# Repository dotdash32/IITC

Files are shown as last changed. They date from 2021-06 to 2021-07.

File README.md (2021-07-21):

# IITC

Intra- and Inter- Tool Changer for Budget 3D Printers

Designed as a mostly printable add-on to the Ender 3 or other V-slot based machines.

The IITC is designed to be cheap to make, widely capable, and easily modifiable.  As such, this Github includes the STLs to print the device, as well as the Fusion 360 files used to create them.

Tech Demo (http://www.youtube.com/watch?v=5y99OYjvCSE)

## Current Progress

The files are currently in development!  While everything *mostly* works on my machine, there are printability and longevity improvements going on.  See the Projects page for a more up to date version of current progress.

## Features

While none of these ideas are completely novel, the combination of these creates a new and very capable machine.

### Intra- Tool Changes

Intra tool changes are between tools on the same tool group, or head.  This is facilitated by the tilting of the head back and forth, and is similar to [MakerTech 3D's Dual Switching Extruder](https://www.makertech3d.com/products/dual-switching-extruder-non-proforge).  Inside a job, this is the most common type of tool change, and is done with just GCode commands.

It rides on bearings for smooth operation and longevity of printed parts.  It uses a kinematic mount, inspired by the [E3D ToolChanger](https://e3d-online.com/pages/toolchanger), but uses socket head cap screws (SHCS) to reduce cost and mounting space.  With entirely standard components, a highly repeatable attachment platform is made.

### Inter- Tool Changes

Inter tool changes are between different tool groups.  These are manually facilitated, allowing the machine to change between different types of tools.  Switching out symmetric nozzles for a dedicated flexible hot end, or mounting a laser engraver or pen plotter.  This is similar to the [XChange](https://www.kickstarter.com/projects/printermods/xchange-v10-hot-swap-tool-changing-for-every-3d-printer) or [Mutant](https://whambamsystems.com/mutant).  However, this combines with the Intra switches to have a more capable machine.

### Tool Ecosystem

The kinematic mount and angle are the same between 1, 2, and 4 position mounts.  Tool groups can still be used on mounts with fewer or more positions, so tool groups are compatible between machines even if they have different numbers of extruders enabled.  This is intended so that a shop with multiple printers can expand flexible capacity without needing to upgrade every mainboard to dual extrusion.

### Remote Tool Changes

A Bowden style servo actuates the tilting motion through a wire rope and spring guides.  The mass of the servo is moved to the rigid frame, thus reducing the mass of the toolhead.  This is inspired by the [Jubilee](https://jubilee3d.com/index.php?title=Main_Page), and uses similar parts.  

### Automatic Z Probing

The kinematic mount gives the Inter tool changes high repeatability, but when spring loaded, the kinematic mount acts like a [Renishaw CNC probe](https://www.renishaw.com/en/kinematic-mounts--25938).  Thus, the nozzle can be used as a probe like a CR-6 and detect any bed surface.

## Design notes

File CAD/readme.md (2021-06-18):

# CAD

The CAD models of the project!

Files are organized by subassembly.
The computer these were designed on is 6 years old and can't handle very large files, so most things are split up for ease of use and modeling.
Each folder contains approximately one assembly with the structure:

```
+-- Assembly_Name_1
|   +-- 0Assembly_Name_1.f3d
|   +-- STL_File1.stl
|   +-- STL_File2.stl
|   +-- readme.md
+ -- Assembly_Name_2
|   +-- ....
+ -- Tools
|   +-- Tool_Name_1
|   |  +-- 0Tool_Name_1.f3d
|   |   +-- STL_File1.stl
|   |   +-- STL_File2.stl
|   |   +-- readme.md
|   +-- Tool_Name_2
|   |   +--...
```

Each folder contains the Fusion archive that was used to make it, so some of these files are `.f3z`, Fusion's interdependent format since they contain derived parts.
Each STL is labelled, but they might not have 1-1 correspondence with Component names.
Instead, there should be nearly 1-1 correspondence on Body names, which is easier for export and managing.

WARNING: Body renaming is still in progress, so it might not be perfect.  If it's unclear, please submit an issue!

Each folder readme should include the needed materials, which will also be compiled in a general spreadsheet to easily build BOMs.  This is a work in progress (yikes), and should also include assembly instructions soon.

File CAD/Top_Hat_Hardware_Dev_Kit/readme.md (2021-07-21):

# Top Hat Hardware Dev Kit

Files related to the Kinematic Mount and creating new tools.  Included are STEP and Fusion files of a simplified mount.
The files contain the `Top_Hat` in it's unmodified form, as well as the infrastructure it mounts to.

The E plate and moving mount are included, but at lower detail so less powerful computers (aka Dotdash's) can create add-ons more easily.
These files are intended to simplify and ease the creation of new tools.
Rather than needing the supply side (Dotdash) to create them, please make your own and pull request them in!

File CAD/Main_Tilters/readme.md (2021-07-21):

# Main Tilters

The main bulk of the project is here, these are what do the dirty work.
There are 3 possible combinations, and each need slightly different materials.

## Common Parts

This topmost section is common to all tilters, so any set of tools can be attached to any tilter.
This is the Kinematic Mount, the set of six screw heads (SHCS) that create a unique resting position for the tool groups mating screws.

### Common Needed Materials

* 1x `Nut_Trap`
* 6x 8mm M3 SHCS
* 6x Thin M3 Nuts

## 1 Position Tilter

This tilter doesn't move, but gives any printer Inter-changes and automatic probing for just a few parts.
Two options, depending on which side of the tool should be used.
This enables a simpler machine to still run complex tool groups, just one tool at a time.

<!-- ![1 Pos Right](/images/1_Pos_Right.png){:width="10px"} ![1 Pos Left](/images/1_Pos_Left.png) -->

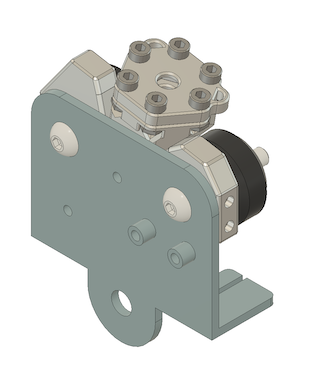
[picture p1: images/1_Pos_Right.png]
1_Pos_Right

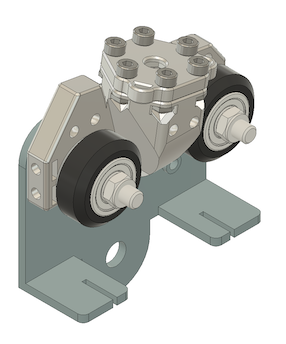
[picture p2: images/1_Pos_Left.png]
1_Pos_Left


### 1 Pos Needed Materials

* 1x `1_Pos_Main_XXX`
  * `_Right` is the near-stock hot end configuration for the Ender 3
  * `_Left` is the `T0` position for the 2 position holder.

Why are there those weird side sections? They extend from the largest flat plane downward, removing the need for supports.

## 2 Position Tilter

This is the mainstay of the project, 2 tools per tool group for intra-switches.

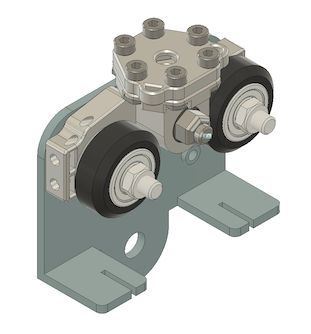
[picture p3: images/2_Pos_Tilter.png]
2 Pos Tilter


### 2 Pos Needed Materials

* 1x `2_Pos_Main`
* 1x `Stationary_Mount`
* 1x `Bearing_Internal_Spacer`
* 1x 25mm M5 FHS
* 2x 105zz Bearings
* 1x Nylock M5 Nut
* 1x 5mm M3 SHCS

### 2 Pos Optional Back Brace

An experimental feature, add 1x `2_Pos_Back_Brace` to potentially stiffen the tilting mechanism.  This is being tested, but requires support and hasn't shown a significant difference in performance yet.

## 4 Position Tilter

This is not finished!
But in order to keep this option open, it needs to be at least partially designed for from the start.
It does not currently have provisions for a tilting cable, but that will hopefully change soon.

This enables front and back tilting as well, so 2 Position Tool Groups will work natively as well.
The issue is that it extends back and would collide with the vertical 2040 beams on the Ender 3.

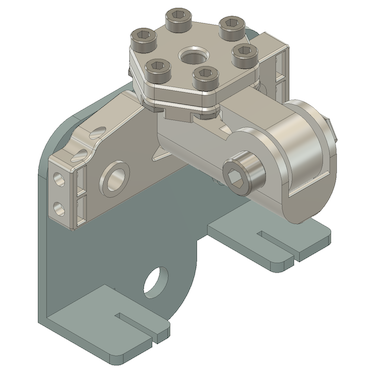
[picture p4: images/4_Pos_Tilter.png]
4 Pos Tilter


### 4 Pos Needed materials

* 1x `4_Pos_Lower`
* 1x `4_Pos_Upper`
* 1x `Stationary_Mount`
* 2x `Bearing_Internal_Spacer`
* 1x 25mm M5 FHS
* 1x 20mm M5 SHCS
* 4x 105zz Bearings
* 2x Nylock M5 Nut
* 1x 5mm M3 SHCS (will probably become 2)

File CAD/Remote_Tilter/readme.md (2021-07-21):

# Remote Tilter

STLs for Remote tilter, uses a servo to actuate the tool change.
Mounts to Nema-17 standard pattern (i.e. to default E3 extruder position)

## 35kg Servo

The current model uses a 35kg-cm servo, which is definitely over powered for the application.  
This is to avoid overheating and failure that was observed in [TeachingTech's Switching Nozzle Video](https://www.youtube.com/watch?v=ag7b9jOhlPY).

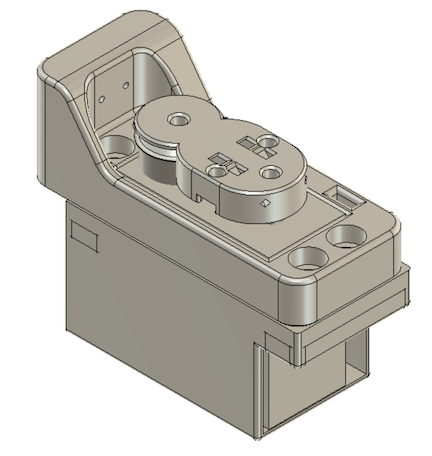
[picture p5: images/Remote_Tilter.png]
Remote Tilter


Future upgrades include testing to switch to a 20kg-cm servo which is half the price, or using a stalled DC motor with current limiting.
Other heat mitigation strategies include a 30mm fan, which has an included duct to redirect the air closely around the servo, or spare stepper motor heat sinks on the metal casing.

### Needed Materials

<!-- TODO: update this in main assembly file. -->

* 1x `Servo_mount`
* 1x `Horn_Top_Attachment`
* Nut mount system
  * 1x `Fanless_Nut_Keeper`

  OR
  * 1x `30mm_Fan_Mount`
  * 1x3010 Fan
* 1x 12mm M3 SHCS
* 5x 8mm M3 SHCS
* 4x Thin M3 Nuts
* 4x 16mm M4 SHCS
* 4x Std M4 Nuts
* 1x Standard Size RC Servo (tested with Annimos 35kg)
* 1x JST to Servo connection Cable
* 2x Spring Guides (from main assembly)

## Direct without Horn

An old version of the servo mount.
It mounts directly to the 25 tooth servo gear, hence the "Direct" name.
Needs either high precision, or to melt the teeth profile in.
This model is harder to work with, so is not fully supported, and is included for the sake of completeness, not convenience.

To melt, something like acrylic cement (for PLA, not recommended plastic) can be used.
Apply the cement liberally to the point of indentation, and then press onto the servo gear.
Let it set until dry, and you have a nice set of embedded teeth!

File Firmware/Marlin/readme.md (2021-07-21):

# Marlin Firmware Setup

## Sample Configs

Dotdash32's configs are available on their fork of [MarlinFirmware](https://github.com/dotdash32/Marlin).  Specifically of interest are the (mostly) updated and designed versions to run this tool changer for the [SKR 2](https://github.com/dotdash32/Marlin/tree/Ender3_skr2) and before it broke, [SKR 1.4T](https://github.com/dotdash32/Marlin/tree/Ender3_skr14Turbo).

There are also bug-fix branches, but are not always updated unless Dotdash has a problem and needs to submit a bug report.

## How to Setup your own Config (1 Position)

These are the key elements to enable in order to get the tool changer up and running.  It's not possible to have an example config for every board (and hard to check if they work on a student budget :\\ ).  While every configuration will be different, these will hopefully give a good guide to get started.  It is recommended that you start with a configuration that works for your printer and controller board BEFORE you start changing things.

This section describes changes needed to enable Inter Changes, switching between different tool groups.  For a single position tool changer (Inter only), follow this section (1 Pos). For a Inter and Intra tool changer, also read the following sections (2 Pos).

Marlin currently only supports up to 2 Positions, since the main element (`SWITCHING_NOZZLE`) only supports 2 positions.  If there is need for more tools (i.e. 4 Position tilter), a more expandable system like RRF or Klipper is ideal, since they can handle secondary control boards.

### Configuration.h (1 Pos)

- Enable Adjustable Temp Sensors

  - `#define TEMP_SENSOR_0 1000` This can then be changed with `M305` in each GCode tool offset file
  
- Adjust Min and Max Temps
  - Change `#define HEATER_X_MINTEMP  nnn` and `#define HEATER_X_MAXTEMP nnn` to reflect the extremes of ALL tools.  This does decrease safety, but is one cost of having only some settings at compile.

- Ensure Thermal Protections

  - `#define THERMAL_PROTECTION_HOTENDS`.  This is really important for safety!  Especially with pluggable hot ends, if a cable is loose, this can prevent fires.

- Probe Settings (For Kinematic Mount Probing)

  - Set Pin (`#define Z_MIN_PROBE_USES_Z_MIN_ENDSTOP_PIN` if using Z end stop)

  - `#define FIX_MOUNTED_PROBE` (technically that or `#define NOZZLE_AS_PROBE`, but that has more restrictions)

  - `#define NOZZLE_TO_PROBE_OFFSET { 0, 0, 0}`, this will be changed by each GCode file (especially the Z offset)

  - `#define Z_AFTER_PROBING 5` or some other value.  This is important to ensure that the tool doesn't switch too close to the bed and smash a tool into the bed

  - `#define Z_PROBE_LOW_POINT -2` or similar value to give some negative travel room

  - `#define Z_AFTER_HOMING 5` like `Z_AFTER_PROBING`, keeps nozzle from smashing into the bed

- Homing and Offsets

  - `#define Z_AFTER_HOMING 5` (it's technically in the homing section of config.h)

  - `#define Z_MIN_POS -2` Allow secondary tools to have a negative Z offset

  - `#define MANUAL_Z_HOME_POS 0` Set home position at probe trigger point

  - `#define Z_SAFE_HOMING` Required for homing with a probe

- SD Card

  - `#define SDSUPPORT` Use an SD card to store tool offset GCode files

### Configuration_adv.h (1 Pos)

- Adjustable Temp Sensors

  - Check Temp Sensor 1000 values, but will be set in GCode files

- SD Card (tool offset folder)

  - `#define SD_PROCEDURE_DEPTH 2`, allow access 1 folder down

  <!-- - `#define SD_MENU_CONFIRM_START` (optional, but incredibly useful, IMO) -->

- Baby Stepping

  - `#define BABYSTEPPING`

  - TODO: `#define BABYSTEP_XY` does this help?

<!-- - Emergency Parser

  - `#define EMERGENCY_PARSER`, Not required, but useful. -->

- Custom Menu

  - Not required, but pretty useful if you need to switch a bunch of hot ends often.

  - Either `#define CUSTOM_MENU_MAIN` or `#define CUSTOM_MENU_CONFIG`

## Intra Tool Changes Config (2 Position)

Further changes needed to enable servo switching of tools (Intra changes).  This does require a controller board capable of driving at least 2 extruder steppers and a servo.

### Configuration.h (2 Pos)

- Enable Switching Nozzle

  - `#define EXTRUDERS 2` Enable dual extrusion

  - `#define SWITCHING_NOZZLE` Specific tool change methodology

  - `#define NUM_SERVOS 1` (or 2 if also using BL Touch)

  - `#define SERVO_DELAY { 150 }` or change to fit your servo's speed

  - `#define EDITABLE_SERVO_ANGLES` This makes it much faster to dial in settings
  
- Enable Adjustable Temp Sensors

  - `#define TEMP_SENSOR_1 1000` Enable second custom thermistor

- Enable Separate PID settings

  - `#define PID_PARAMS_PER_HOTEND` Allow non-symmetric hot end control loops

  - Change `DEFINE_Kn_LIST` to 2 entries for each of the three settings.

- Enable second extruder

  - `#define E1_DRIVER_TYPE` to be whatever is in your controller board.

  - `#define DISTINCT_E_FACTORS` for non-symmetric extruders

  - Update "default values" to include 5 values.  There are several, so be sure to check them all.

    - `DEFAULT_AXIS_STEPS_PER_UNIT`

    - `DEFAULT_MAX_FEEDRATE`

    - `DEFAULT_MAX_ACCELERATION`

### Configuration_adv.h (2 Pos)

- Tool Change Raise

  - `#define TOOLCHANGE_ZRAISE 2` or other setting to clear any parts

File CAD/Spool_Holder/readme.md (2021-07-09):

# Spool Holder

Colloquially called the "Spool Whale" because of the whale tail like design, a purpose built dual spool holder with provisions for in line filament runout sensors and dual Creality style extruders.

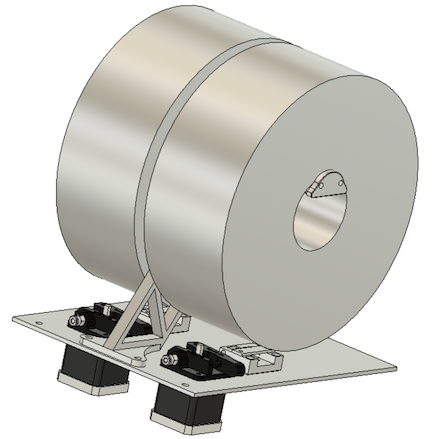
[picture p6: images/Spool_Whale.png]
Spool Whale


## Base Holder

Simple holder, includes two extruder mounts (Creality MK10 style) and dual roll filament holder.

This also adopts the PTFE liner from Voron, so that spools are not in contact with printed plastic, but instead slippery PTFE during printing.

### Needed Materials

- `Bottom_Board_Small` (dxf to be laser cut)
  - printable STL Coming Soon
- `Spool_Whale_Lower`
- `Spool_Whale_Upper`
- 2x 12mm M5 SHCS
- 2x M5 T nuts (from stock spool holder)
- 3x 12mm M3 SHCS
- 3x M3 thin nuts
- 2x Creality Extruders (steppers, extruder tops)
- 2x Bowden Tubes

## Optional Filament Runout Sensors

This is for one sensor, so for two, double everything.

### Needed materials

- `Fil_Runout_Bottom`
- `Fil_Runout_Top`
- 4x 12mm M3 SHCS
- 4x M3 thin nuts
- Short PTFE tube
- Microswitch with roller lever
- Wiring harness

There are some printability problems with the filament runout sensors relating to the Bowden tubes, so be warned.

Also, an upgrade to BMG style extruders is soft-planned for higher performance.

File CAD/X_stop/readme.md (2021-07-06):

# X Stop

A modified X limit switch holder to increase clearance.

The stock Ender 3 X stop has a QR code and sticks out really far.  This is a clearance problem for some dual extruders, since the part needs to swing out of the way during tool changes.

### Needed Materials

- 1x `Slim_X_Stop`
- 1x X stop micro switch
- 2x 5mm M3 SHCS
- 4x 25mm M3 Flat Head Screws

## Supported Version

Older version that needs support to print.
This model is more useful if you only have short SHCS (I had an Amazon mixed bag for prototyping) on hand, but otherwise, use the more updated version and the countersunk screws.

### Needed Materials

- 1x `Slim_X_Stop_Support`
- 1x X stop micro switch
- 2x 5mm M3 SHCS
- 4x 12mm M3 SHCS

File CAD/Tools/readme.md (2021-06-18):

# Tools

Different tool heads for the IITC

## Included Options:

### Common

Common tools between all options.

- `Camera_mount`: Mount for 5mm Borescope with provisions for cable management at the top.  Requires support.

- `Triple_springs`: adapt 3 light springs (McMaster #9657K622) for heavier tools.

### Single_Hero_Me

Mount for a single extruder (1Pos style).  It adapts the Hero Me Gen 3 and 9-pin D sub connector.  Mounts Creality style hot end nearly in line with original position, moves a few mm forward in Y.  No loss of X travel.

### Double_Hero_me

Mount for double extruder (2Pos style).  Adapts Hero Me Gen 3 and mirrors across to get two extruders with an approximate 38mm offset.  Uses 2 Creality hot ends and has special fan duct to avoid collisions.

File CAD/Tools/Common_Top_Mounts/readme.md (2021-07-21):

# Common Tools - Top Mounts

Common tools to mount a tool group to the base pivot.  These usually hold springs to allow for auto Z probing.

## Triple Springs Static

Adapter to use 3 McMaster #9657K622 springs for a heavier tool.

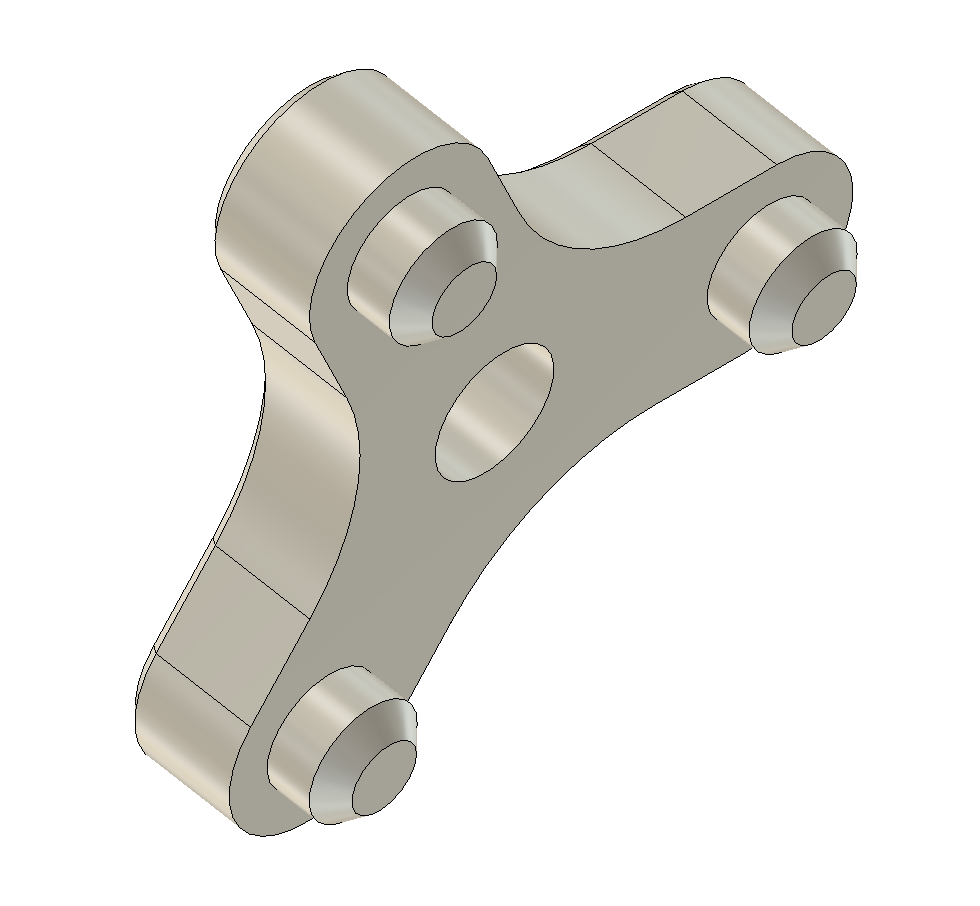
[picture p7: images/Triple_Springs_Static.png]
Triple Springs Static


### Needed Materials (Static)

- 1x `Triple_Springs_Static`
- 3x .375x.300 springs (McMaster #9657K622)
- 1x 30mm M5 (for connecting to Kin Mount)
- 1x M5 nylock nut (for connecting to Kin Mount)

## Triple Springs Adjustable

Adapter to use 3 McMaster #9657K622 springs for a heavier tool, but allow uneven forward/back tension.  This is intended to account for 2 Position tool groups, where there is significant weight on the front of the carriage, but none in the back.

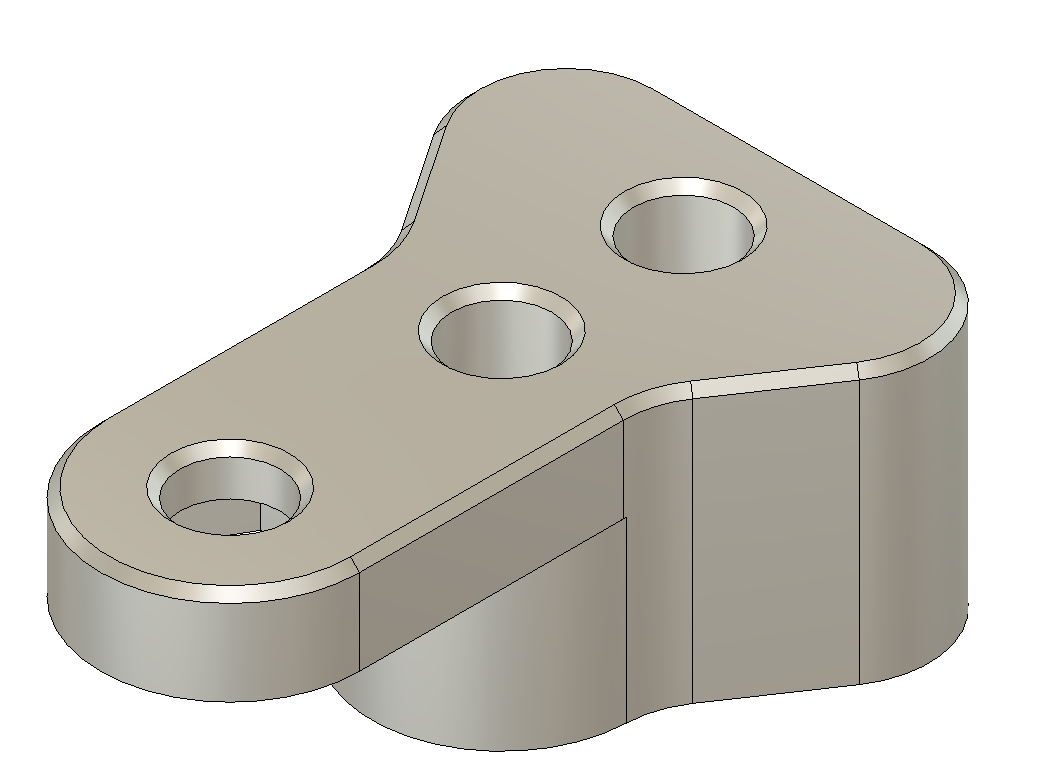
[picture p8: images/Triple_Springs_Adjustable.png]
Triple Springs Adjustable


Primary tension is adjustable with the main screw, tightening the back two springs.  Front tension is adjustable with separate jam nuts.

### Needed Materials (Adjustable)

- 1x `Triple_Springs_Adjustable`
- 3x .375x.300 springs (McMaster #9657K622)
- 1x 30mm M5 (for main connection to Kin Mount)
- 1x 20mm M5 (for rear connection to Kin Mount)
- 1x 16mm M5 (for front tension adjustment)
- 1x M5 nylock nut (for main connection to Kin Mount)
- 4x M5 thin nut (tension adjustment)

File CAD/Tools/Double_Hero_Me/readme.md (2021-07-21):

# Double Hero Me

Dual Extruder mount for 2 Creality MK8 Style hot ends

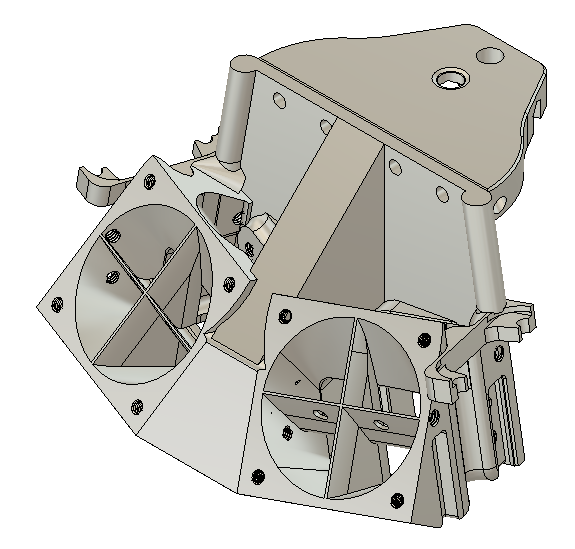
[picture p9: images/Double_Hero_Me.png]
Double_Hero_Me


## Caveats

This is sort of a legacy tool group, stitched together quickly for expedited testing.  It absolutely works, but most things are at slight angles, and the hot end mount on the right isn't the same length to the D-sub connector.  It is harder to print (support needed), and the fans are not optimized.

### Needed Materials

- 1x `Hotend_Mount`
- 1x`Top_Hat`
- 2x Creality MK8 Hot ends
- 2x 40mm Fan
- 2x Bowden tubes
- 1x `Dsub_Cap_left`
- 1x `Dsub_Cap_right`
- 2x 9 Pin D sub connectors (male)
- 1x `Fan_Duct`
- 2x 4010 Blower fans (part cooling)
- 4x 8mm M3 SHCS
- 3x 5mm M3 SHCS
- 4x 16mm M3 SHCS
- 7x Thin M3 nuts

## Hot End Modifications

To have quick change-ability for PTFE lined hot ends, it is recommended to do the "washer fix" that adds a section of captive PTFE tube inside the hot end, trapped below a washer.  This allows the Bowden tube above the washer to be easily removed without worrying about perfectly re-seating the tube after an Inter tool change.

Originally by Luke Hatfield, [CHEP has a video](https://www.youtube.com/watch?v=7tCxO17XZtw) about it, and you can find the necessary files on [Thingiverse](https://www.thingiverse.com/thing:3203831).  The fix can also improve printing overall, so its recommended to do.

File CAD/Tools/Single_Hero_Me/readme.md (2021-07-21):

# Single Hero Me

Adapted Hero Me V3 mount to mount a single Creality MK8 hot-end to the Kinematic Mount.

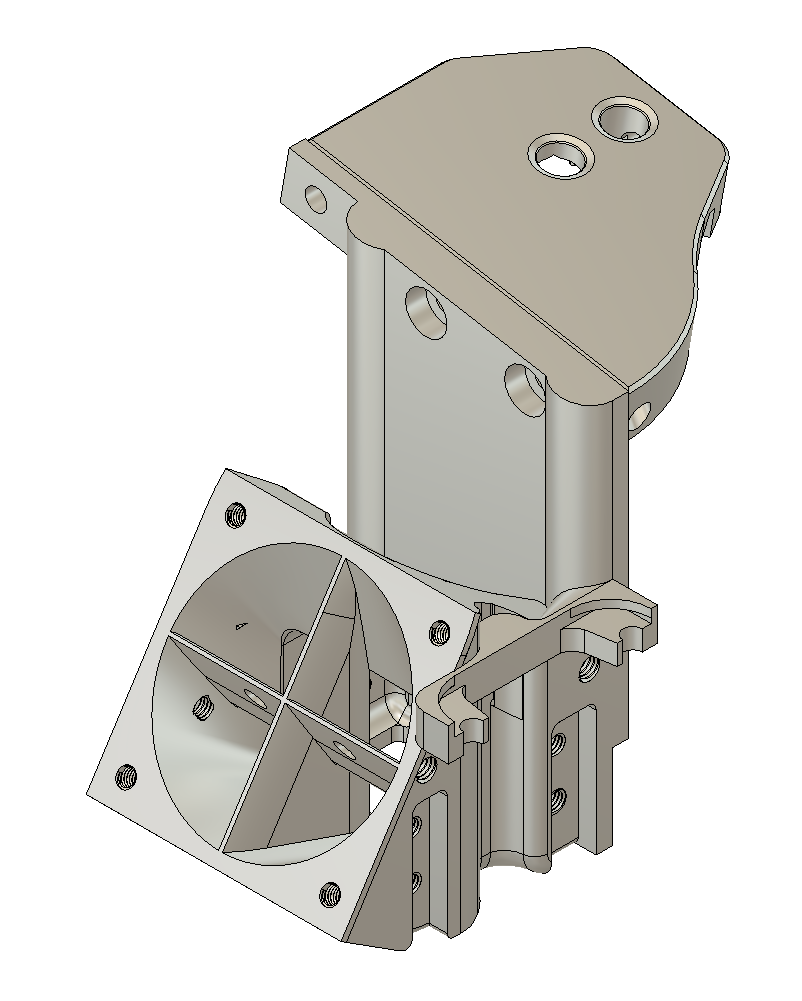
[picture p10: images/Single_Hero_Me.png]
Single Hero Me


## Caveats

This is not optimized for support-less printing, like the main Hero Me.  

### Needed Materials

- 1x`Hotend_Mount`
- 1x `Kinematic_Mount`
- 1x Creality MK8 Hot ends
- 1x 40mm Fan (hot end cooling)
- 1x Bowden tubes
- 1x `Dsub_Cap`
- 1x 9 Pin D sub connectors (male)
- 1x `Symmetric_Duct`
- 1x 4010 Blower fans (part cooling)
- 3x 8mm M3 SHCS
- 3x 5mm M3 SHCS
- 2x 16mm M3 SHCS
- 6x Thin M3 nuts

## Hot End Modifications

To have quick change-ability for PTFE lined hot ends, it is recommended to do the "washer fix" that adds a section of captive PTFE tube inside the hot end, trapped below a washer.  This allows the Bowden tube above the washer to be easily removed without worrying about perfectly re-seating the tube after an Inter tool change.

Originally by Luke Hatfield, [CHEP has a video](https://www.youtube.com/watch?v=7tCxO17XZtw) about it, and you can find the necessary files on [Thingiverse](https://www.thingiverse.com/thing:3203831).  The fix can also improve printing overall, so its recommended to do.

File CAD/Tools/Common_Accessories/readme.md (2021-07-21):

# Common Tools - Accessories

Common tools that mount to the side of the `Stationary_Mount` with 2 M3 screws on 10mm spacing

## Camera_Mount

Mount for 5mm borescope with cable management options at the top.  Mounts to side of Stationary Mount.

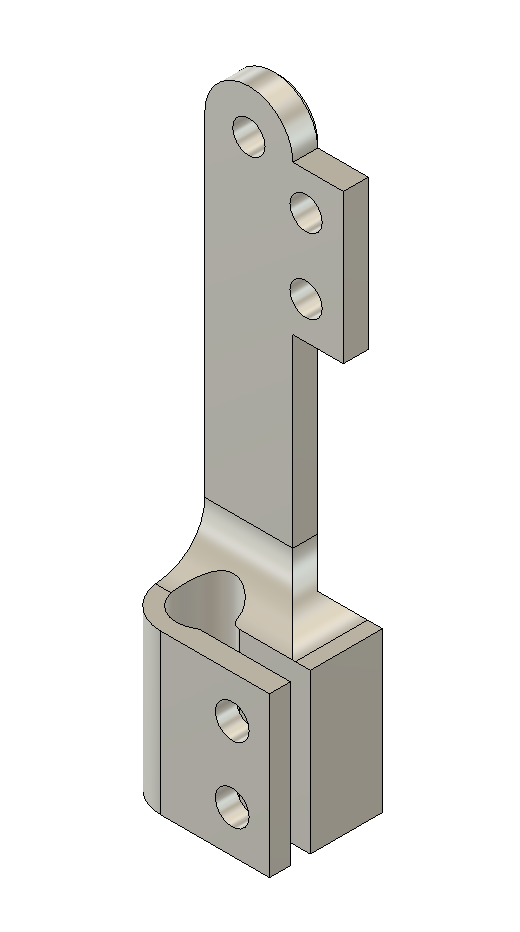
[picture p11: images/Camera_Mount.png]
Camera Mount


### Needed Materials

- 1x `Camera_Mount.stl`
- 2x 12mm M3 SHCS
- 2x M3 nuts
- 2x 8mm M3 SHCS (for mounting to SM)

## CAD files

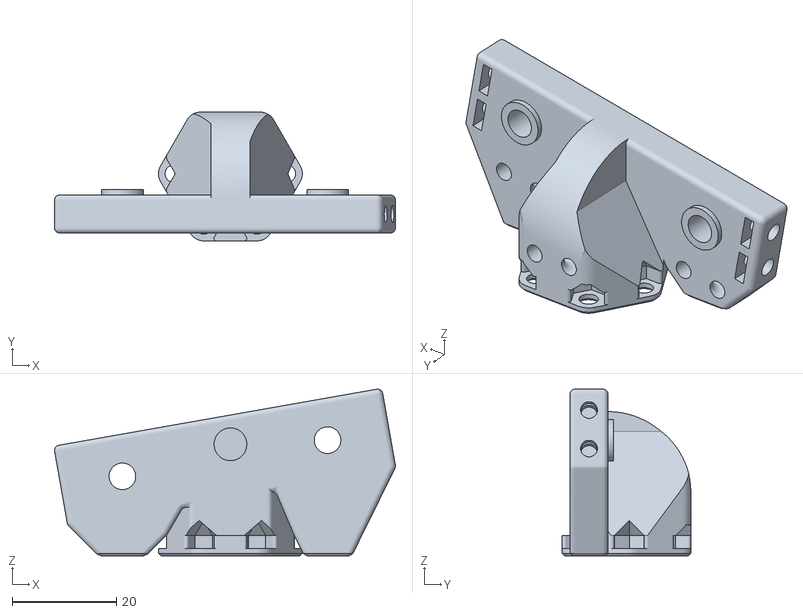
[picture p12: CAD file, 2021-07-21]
CAD/Main_Tilters/1_Pos_Main_Right.stl
65.5 x 24.8 x 32.0

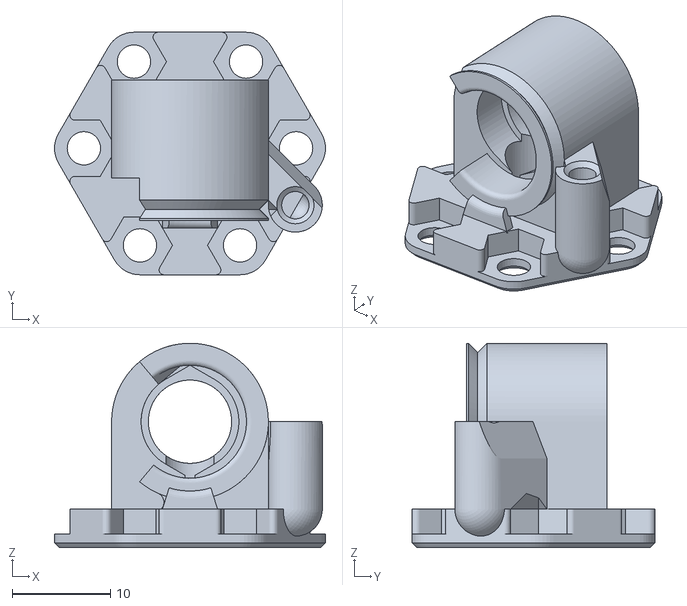
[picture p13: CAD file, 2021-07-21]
CAD/Main_Tilters/2_Pos_Main.stl
27.7 x 24.8 x 20.9

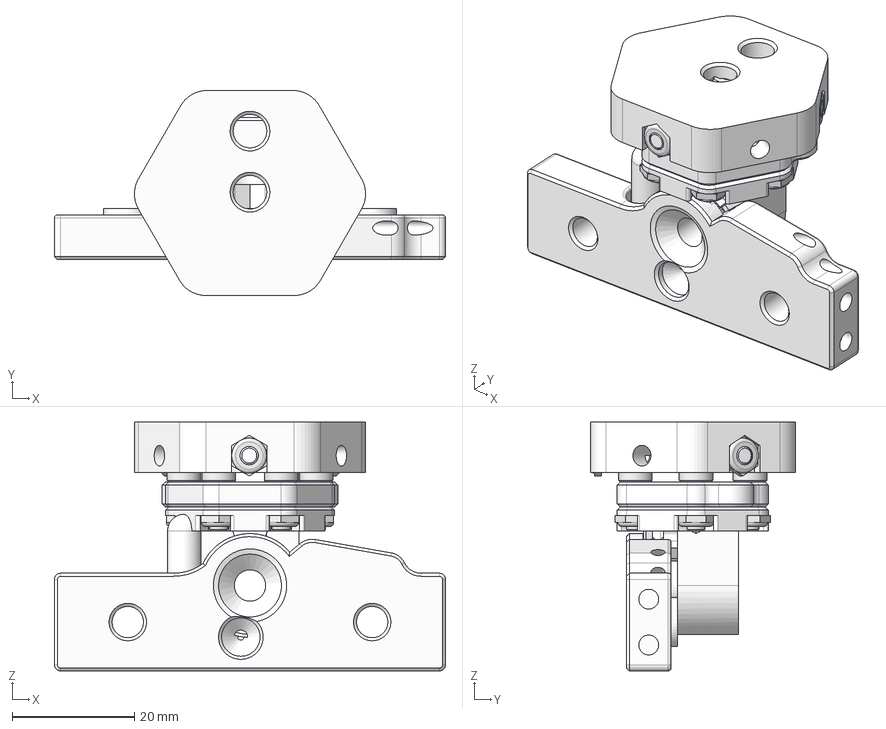
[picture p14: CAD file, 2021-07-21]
CAD/Main_Tilters/0Main_Tilters.step
64.0 x 33.6 x 40.7 mm
Main Pivot
KinBolt x 6
KinNut x 9
Stationary Mount
Generic Hat
KinBoltShort x 3
HDK

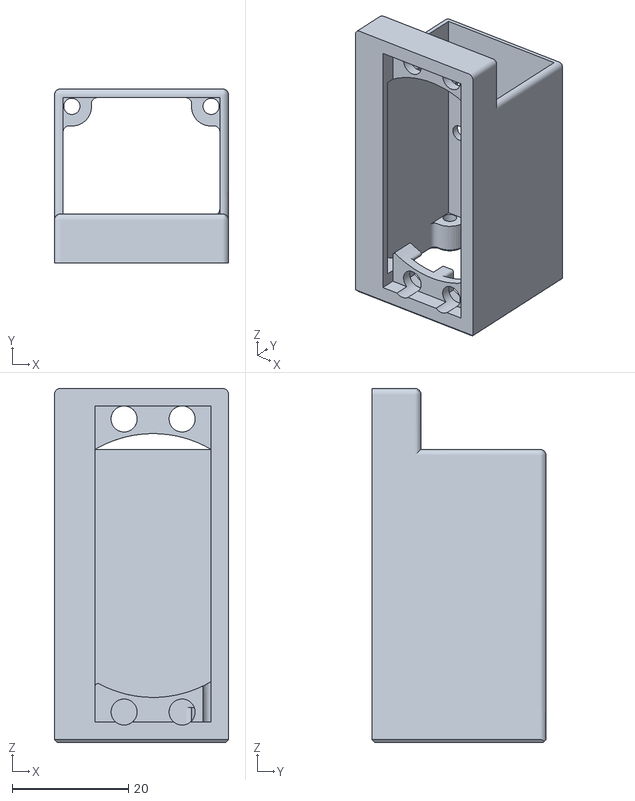
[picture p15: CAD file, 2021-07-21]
CAD/Remote_Tilter/30mm_Fan_Mount.stl
30.0 x 30.0 x 61.0

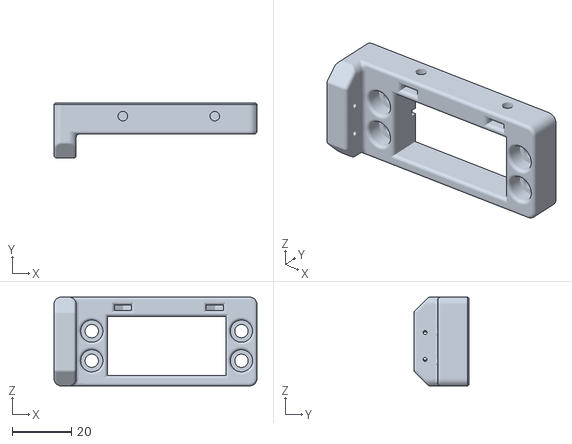
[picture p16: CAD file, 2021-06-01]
CAD/Remote_Tilter/Direct_without_horn/Direct_Servo_Mount.stl
68.5 x 18.7 x 30.0

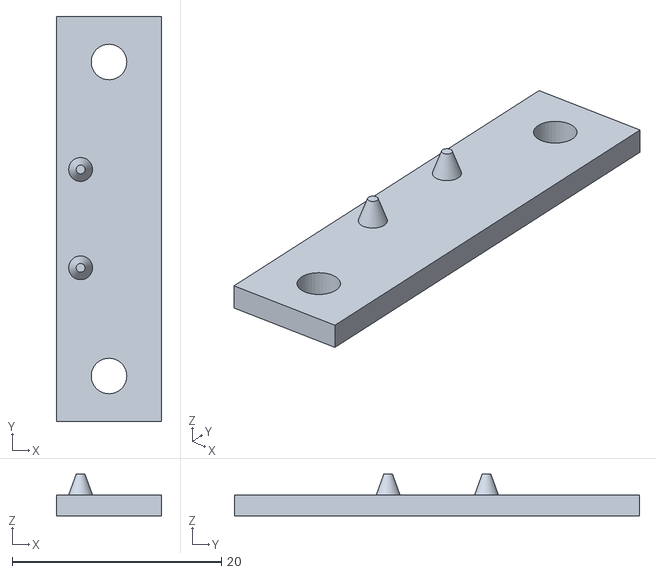
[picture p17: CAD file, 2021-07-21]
CAD/Spool_Holder/Fil_Runout_Top.stl
10.0 x 38.7 x 3.98

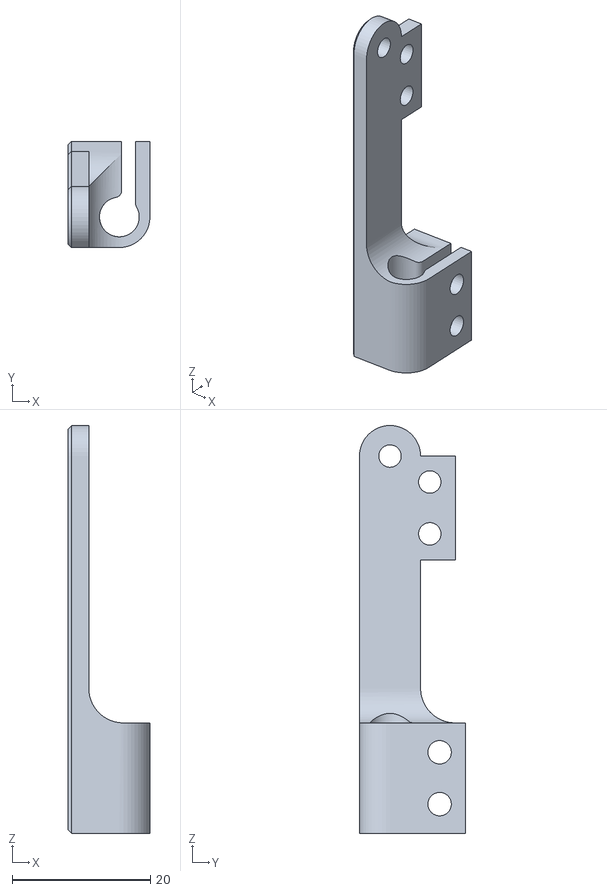
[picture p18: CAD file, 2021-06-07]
CAD/Tools/Common_Accessories/Camera_Mount.stl
11.8 x 15.4 x 59.0

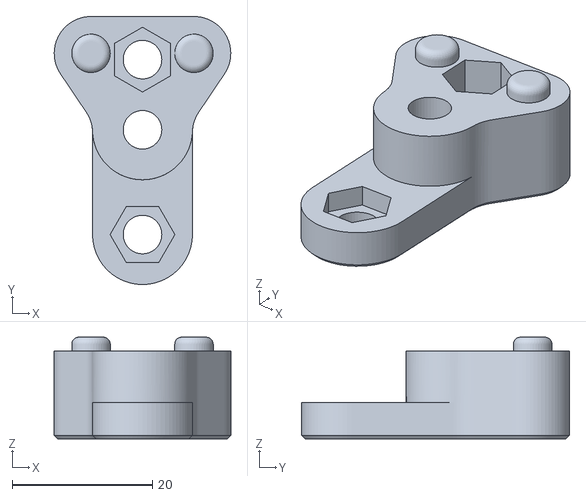
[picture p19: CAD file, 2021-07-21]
CAD/Tools/Common_Top_Mounts/Triple_Springs_Adjustable.stl
25.2 x 38.2 x 14.5

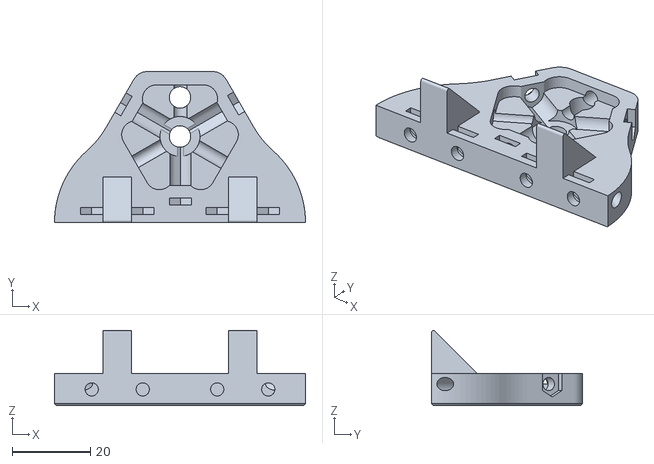
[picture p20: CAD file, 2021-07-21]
CAD/Tools/Double_Hero_Me/Top_hat.stl
64.3 x 38.7 x 19.2

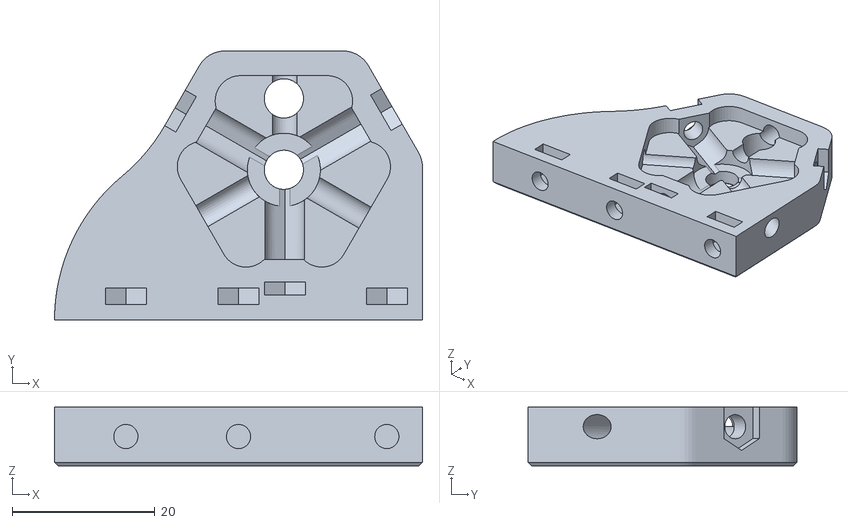
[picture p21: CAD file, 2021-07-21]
CAD/Tools/Single_Hero_Me/Kinematic_Mount.stl
51.6 x 37.7 x 8.25

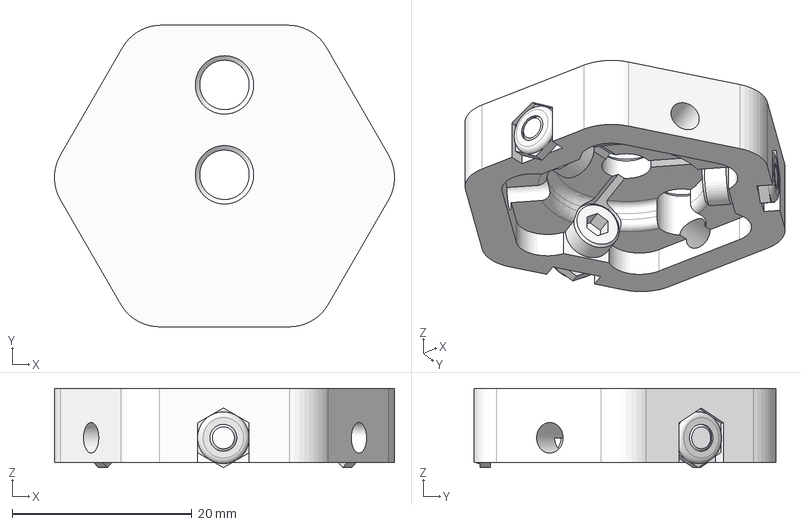
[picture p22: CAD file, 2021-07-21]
CAD/Top_Hat_Hardware_Dev_Kit/0Top_Hat_with_HDK.step
37.8 x 33.6 x 8.82 mm
Generic Hat
KinNut x 3
KinBoltShort x 3
HDK

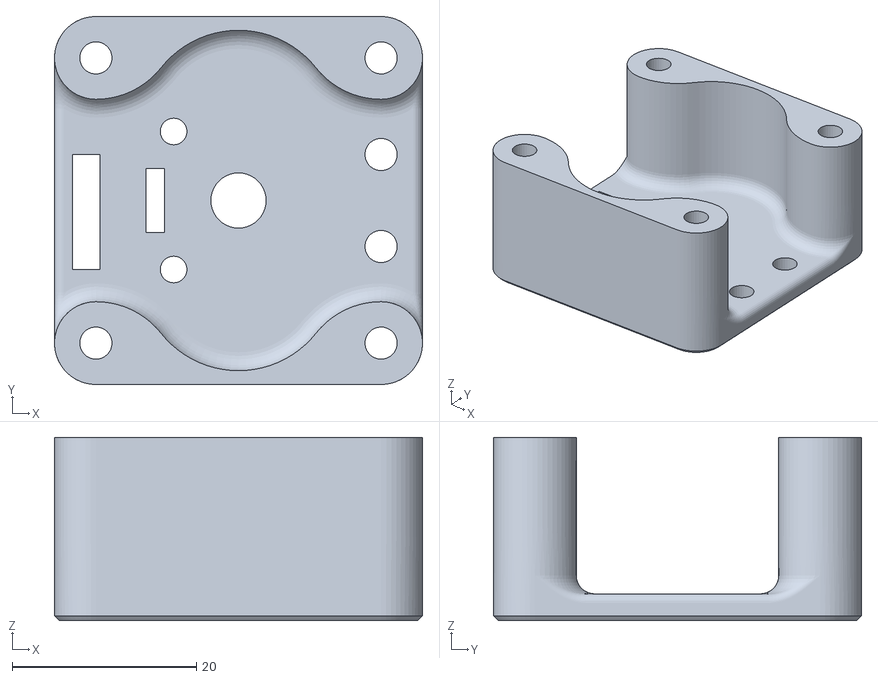
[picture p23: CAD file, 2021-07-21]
CAD/X_stop/Slim_X_Stop.stl
40.0 x 40.0 x 19.9

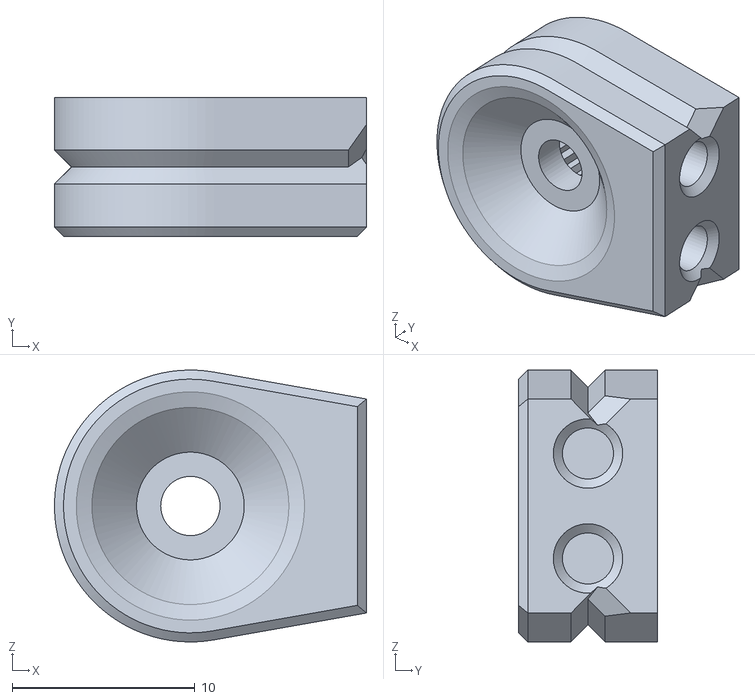
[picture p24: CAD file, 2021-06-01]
CAD/Remote_Tilter/Direct_without_horn/Direct_Servo_Horn.stl
17.1 x 7.60 x 14.9

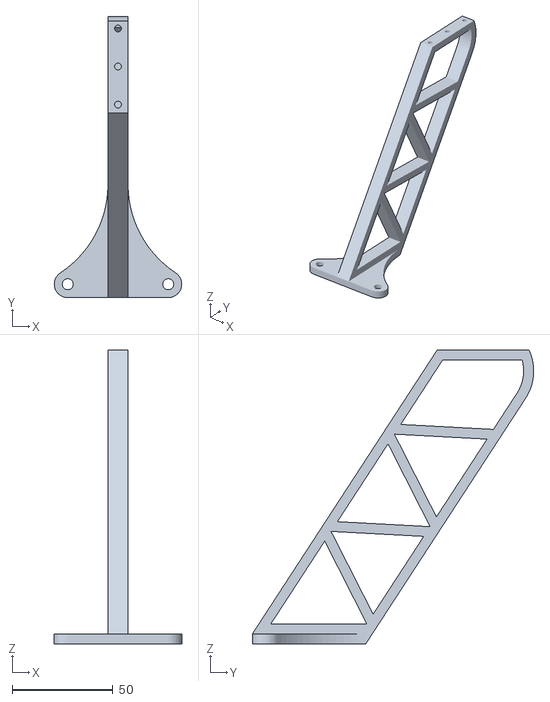
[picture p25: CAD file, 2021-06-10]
CAD/Spool_Holder/Spool_Whale_Lower.stl
63.4 x 140.0 x 146.3

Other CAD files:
CAD/Main_Tilters/1_Pos_Main_Left.stl
CAD/Tools/Common_Top_Mounts/Triple_springs_Static.stl
CAD/Tools/Double_Hero_Me/Fan_Duct.stl
CAD/Tools/Single_Hero_Me/Symetric_Duct.stl
CAD/Main_Tilters/0Main_Tilters.f3d
CAD/Main_Tilters/2_Pos_Back_Brace.stl
CAD/Main_Tilters/4_Pos_Lower.stl
CAD/Main_Tilters/4_Pos_Upper.stl
CAD/Main_Tilters/Bearing_Internal_Spacer.stl
CAD/Main_Tilters/Generic_Hat.stl
CAD/Main_Tilters/Nut_Trap.stl
CAD/Main_Tilters/Stationary_Mount.stl
CAD/Remote_Tilter/0Remote_Tilter.f3d
CAD/Remote_Tilter/0Remote_Tilter.step
CAD/Remote_Tilter/Fanless_Nut_Keeper.stl
CAD/Remote_Tilter/Horn_Top_Attachment.stl
CAD/Remote_Tilter/Servo_Mount.stl
CAD/Spool_Holder/0Spool_Holder.f3d
CAD/Spool_Holder/Bottom_Board_Small.dxf
CAD/Spool_Holder/Fil_Runout_Bottom.stl
CAD/Spool_Holder/Spool_Whale_Uper.stl
CAD/Tools/Double_Hero_Me/Dsub_Cap_left.stl
CAD/Tools/Double_Hero_Me/Dsub_Cap_right.stl
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

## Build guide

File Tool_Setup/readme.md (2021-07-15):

# Tool Setup

This folder includes files related to Tool setup.

See the [Tool Setup Procedure](/Tool_Setup/Tool_setup_procedure.md) for a walk through of how to setup a tool, which links to the example GCode for a [pen plotter](/Tool_Setup/PlotterHead.gcode).  Additionally, see the [Selected GCode Reference](/Tool_Setup/Selected_Gcode_Reference.md) for commonly used GCodes during individual tool groups.

This folder mainly acts as a space to store all Dotdash's personal tool offsets, and track them.  They are stored in here and also on the printer SD card.  Specifically, the extension [FileSync](https://marketplace.visualstudio.com/items?itemName=CatStarwind.filesync) is used to keep the subfolder `Tool_Files` in sync with the SD card.  This is certainly handy to set up on everyone's personal forks, but might not be overly useful.  It does require creating a new VSCode workspace path to the folder to work.

## Calling Tool Offsets

To use separate GCode files like above, there are some config changes needed in Marlin.  

- Enable `SDSUPPORT`
- Set `SD_PROCEDURE_DEPTH` to 2
- Create file structure on SD Card

The file structure that has worked is below.  While not necessary to have a separate folder, it does keep everything organized, and easier to clean out the SD card if it gets full of prints.

```none
SD Card
.
+-- 0TOOLS
|   +-- DualCreality.gcode
|   +-- PlotterHead.gcode
|   +-- OtherTools1.gcode
|   +-- OtherTools2.gcode
|   +-- ...
|   +-- OtherToolsN.gcode
+-- PrintJob1.gcode
+-- PrintJob2.gcode
+-- ...
+-- PrintJobN.gcode
```

`M32` can be used to call a specific program, and using the `P` flag allows the printer to continue to run a job.  So in your start GCode you might put `M32 P !/0TOOLS/FILE.GCO#`, replacing `FILE.GCO` with the output from `M20`.  Since this command uses DOS 8.3 filenames, it can be hard to read, so keeping filenames distinct is important.

### Useful Commands

- `M20` List SD Card contents (`L` includes long filename, which is more human readable)
- `M32` Run file (`P` sets subprogram, so another command can be called afterward)
- `M21` Attach SD Card (needed to see files from printer)
- `M22` Release SD Card (needed to see files from computer as external disk, if enable by boot-loader)

## FileSync

Using the [FileSync](https://marketplace.visualstudio.com/items?itemName=CatStarwind.filesync) extension allows a Github synced set of Tool offset GCode files to be also stored on an SD card.  It is very useful to have some sort of MSC (access SD card like an external storage device from your computer) for this to work efficiently.  Steps to set up:

1. Download and install the extension (from VSCode extension manager)

2. Ensure the `.code-workspace` file includes a path directly to the Tool Offset folder of interest

    - for example:

    ```code-workspace
    {
        "path": "./Tool_Setup/Tool_Files"
    },
    ```

3. Edit the VSCode `settings.json` file to meet the Source/Destination specs of the Extensions

    - for example:

    ```json
    "filesync.mappings": [
        { "source": "/PATH_TO_IITC_REPO/Tool_Setup/Tool_Files", 
            "destination": "/Volumes/SKR_14T/0tools"} 
    ],
    ```

4. Double check everything is working by looking at the FileSync output from the VSCode terminal

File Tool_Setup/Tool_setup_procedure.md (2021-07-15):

# Tool setup Procedure

Caveats:

`T0`, the original tool, often called Extruder 1 in firmware, is active when homing.  This means that it's "deployed" position cannot interfere with X/Y end stops.

For this reason, the standard position is `T0` as X_MIN and Y_MIN tool. This moves the tool out of the way of X_MIN (on an i3 bed slinger) during homing, but this might change depending on your machine.  Change your servo positions to correct this and chooser a `T0` that does not interfere with end stops triggering.  The Slim_X_Stop also helps with this problem (on an Ender 3).

Another element for standardization is software ordering.  Since most of the software for 3D printing (that I've seen at least) uses a writing system that goes left to right, `T0` is always on the left.  Thus, when looking at a printer head on, the first tool should follow this format.  From a UX perspective, this means that the tools will respect Marlin's Heater ordering, and Cura's Extruder ordering.

A caveat to using this convention and also supporting 1 Position base mounts is that the most "exotic" or unusual extruder should be placed such that when using a single tool machine, it can be used.  For example, on a machine with a standard flow and high flow nozzle, the high flow should be in position 2 (`T1`), such that when placed on a non-inter-switching machine, that nozzle can be used more readily.

`T1`, `T2`, and `Tn` are subsequent tools, up until `n=6`, the maximum number supported in Marlin.  The IITC supports 1, 2, or 4 (coming soon) tools, but the `Tn` nomenclature is used to generalize the procedure.

## Useful Commands

- `M206` Home offset

- `M218` Tool offset

- `M851` Probe Offset

## Find X/Y of First Tool

1. Home Machine (at least XY)

2. Jog T0 to ideal X0 Y0 Position

    - This is likely the lower right corner of the bed

3. Set this position as `M206` Home offset

   - Usually need to invert the signs

   - If tool cannot reach X0 Y0, use an offset guide to find the “theoretical limits”.  Soft end stops should still respect the physical limits of your machine.

   - Set this same Position as XY Probe offset in `M851` if using Marlin 2.0.8.0 or lower

4. Ensure the machine now homes Z in proper location

   - If `Z_SAFE_HOMING` is enabled, should be in true center of bed

5. Check that the Soft Limits are correct with `M211`

   - Also good to jog to limits and make sure you cannot over travel!

## Find Z offset of First Tool

1. Reset Probe Z height with `M851 Z0`

2. Get a thin sheet place it under the homing probe position

   - Paper or shim stock is ideal for this.  You should measure the paper before hand, but most paper is around 0.004" or .1mm thick.

3. Home machine in Z (`G28 Z`)

4. Step up the Z until the paper just clears

   - See the exact Z position with `M114`.

5. Record this value in `M851 Z`

   - E.g. if you measure Z0.6 when the nozzle clears, record `M851 Z0.6`.

## Find Rough X/Y offset of Subsequent Tools

For the purposes of `Z_SAFE_HOMING` and probe sensitivity, I find it useful to roughly center the tool on the bed before probing.  This is primarily an artifact of my Ender 3 bed being unstable at the corners though.

1. Move to a clean section of the bed that is sufficiently rigid

   - Single rail V slot beds can be wobbly at the edges, better to move towards the center.

   - Using a round position (ie `X100 Y100`) will make this easier later

2. Create a mark with `T0`

   - for pen tools, a little dot is easy

   - For hot ends, paper and a little indent also works well

   - Soft powder or clay is useful, get any sort of indent.  You can also reform it to restart the process

3. Switch to Tool x (ie `T1` or `Tn`)

   - Be sure there is enough Z clearance before you change tools!  Consider bringing `T0` up ~5mm.

4. Jog to the approximate location

5. Record the difference in initial position and final position in `M218 Tn X Y`

   - `M114` recalls position

   - Use (Original Position) - (New Position)  to get the offset

   - To avoid moving away from the initial mark, switch back to `T0`, then apply the offset.  Be aware of Z clearance!

6. Check the ballpark estimate by switching back and forth

   - It's often useful to Home (`G28`), as the offset is applied to the current position, causing the `T0` offset to be pushed away from the initial mark.

   - This can be mitigated with by switching to `T0` then applying the offset, but it's easier to just re-home between switches

7. Repeat until you are satisfied with the rough offset.  This is rough, it just needs to be close, we'll fine tune it later.

## Find Z offsets of Subsequent Tools

<!-- Weird edge case: in vanilla (first pass) Marlin, the probing tool needs to be the lowest one.  This seems whack, so what if we use CNC coordinate systems to work around this and use a different offset?  (this has since been solved)-->

<!-- CAVEAT: `T1` must be LOWER than `T0` for this to work.  The first Tool must be the highest tool.  A workaround might be possible, or just design your tools better. -->

For maximum Z height flexibility, you want to define the `Z_MIN_POS -2` and `MANUAL_Z_HOME_POS 0`.  This lets any tool travel below the probe trigger point, within reason.  Since the IITC is designed to have one of the tools itself probe, so long as there is no significant mismatch in tool lengths, this should work.  Otherwise, increase the tolerance on `Z_MIN_POS`.

1. Home Z of first tool

2. Reset any offset with `M218 T1 Z0`

3. Move `T0` up until there will be sufficient clearance for tool change

4. Move the new tool down until it is zeroed

   - Use a piece of paper or shim stock for this, like in First Tool Z offsetting

5. Take the negative of this to use for `M218 Tn Z`

   - Easiest way to check the offset is to remember the number, switch back to `T0`, then apply new offset.  When switching back to `T1`, the offset will be applied and `T0` shouldn't slam into the bed.

6. Verify this offset with a test print.  

   - One strategy is to print 2 rectangles as a pseudo skirt with sufficient space between them.  It should print one, and then the other, allowing baby stepping while printing to dial in the height offsets of both tools.

     - 0 top/bottom layers
     - 0% infill
     - 10 perimeters
     - 1 layer thick
     - 10mm spacing between squares

The Z offset is probably more important than the X/Y offset for successful printing!  This needs to be dialed in well, or layers will not stack on top of each other well.  This can lead to de-lamination of support structures or overall bad part quality.  Take your time, and make sure the tools provide even layers.

## Fine Tune X/Y offset of Subsequent Tools

Cura's [Calibration Shapes](https://marketplace.ultimaker.com/app/cura/plugins/5axes/CalibrationShapes) plugin has a dual extruder calibration print, which is quite handy.  Be sure to disable Brim when printing.

### Pen tools

 draw some lines, fine tune the X/Y offsets

 Draw a line in X with both tools, then measure the offset between them.  Repeat and fine tune the offset.  Do the same in Y.

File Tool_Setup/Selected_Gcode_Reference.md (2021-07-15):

# Selected GCode Reference

A few GCodes that are relevant for setting up different hot ends and extruders.  You should always check your Firmware reference ([Marlin](https://marlinfw.org/meta/gcode/), [RRF](https://duet3d.dozuki.com/Wiki/Gcode), [Klipper](https://www.klipper3d.org/G-Codes.html)), but this guide is mainly written for Marlin users.  Tools can be referenced by running subprograms (detailed in the parent [readme](/Tool_Setup/readme.md)), overwriting the base configuration.  Since RRF and Klipper support modular config files, it might make more sense to just edit the config file and restart the printer.

These are just a few settings, and this is not a comprehensive guide.  It can serve as a checklist of things to ensure you have all the necessary parameters changed for a new tool, but you should always consult the documentation to understand the command.  This is just a starting point!

## Tool Change

- `M280` Set servo angle, needs `Pn` index and `Snnn` angle
- `M281` Set servo up/down angle, needs `Pn` index and `Unnn`/`Lnnn` upper/lower limits
- `Tn` Change Tools, `n` = [0,6]

## Tool Offsets

- `M206` Home offset, set `T0`'s `G28` position relative to actual edge of bed
- `M218` Tool offset, set `Tn` position relative to `T0`
- `M851` Probe offset, set `T0` Z offset
- `M114` Report Position

## Extruder Options

- `M92` Set steps per unit (`Tn Exxx`)
- `M201` Set max acceleration (`Tn Exxx`)
- `M203` Set max feed rate (`Tn Exxx`)
- `M301` Set hot end PID (`En Pnnn Innn Dnnn` {`Tn` => `En`})
- `M305` Set Custom Thermistor Parameters (`Pn Bnnn Rnnn Tnnn` {`Tn` => `Pn`})

## Communication

- `M117` Display a message on LCD
- `M150` Set LED color (requires LED strip/Andon)

## EEPROM

- `M500` Save Settings (save to EEPROM)
- `M501` Restore Settings (load from EEPROM)
- `M502` "Factory" Reset (load from firmware)
- `M503` Report settings (echo all settings)

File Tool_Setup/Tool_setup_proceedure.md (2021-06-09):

# Tool setup Proceedure:

Caveats: 

`T0`, the original tool, often called Extruder 1 in firmware, is active when homing.  This means that it's "deployed" position cannot interfere with X/Y endstops.

For this reason, the standard position is `T0` as Xmin and Ymin tool. This moves the tool out of the way of Xmin (on an i3 bedslinger) during homing, but this might change depending on your machine.  Change your servo positions to correct this and chooser a `T0` that does not interfere with endstops triggering.

`T1`, `T2`, and `Tn` are subsequent tools, up until `n=6`, the maximum number supported in Marlin.  The IITC supports 1, 2, or 4 (coming soon) tools, but the `Tn` nomenclature is used to generalize the proceedure.

## Useful Commands

- `M206` Home offset

- `M218` Tool offset

- `M851` Probe Offset

## Find X/Y of First Tool

1. Home Machine (at least XY)

2. Jog T0 to ideal X0 Y0 Position

	- This is likely the lower right corner of the bed

3. Set this position as `M206` Home offset

	- Usually need to invert the signs

	- If tool cannot reach X0 Y0, use an offset guide to find the “theoretical limits”.  Soft endstops should still respect the physical limits of your machine.

	- Set this same Position as XY Probe offset in `M851` if using Marlin 2.0.8.0 or lower

4. Ensure the machine now homes Z in proper location

	- If `Z_SAFE_HOMING` is enabled, should be in true center of bed

5. Check that the Soft Limits are correct with `M211`

	- Also good to jog to limits and make sure you cannot over travel!

## Find Z offset of First Tool

1. Reset Probe Z height with `M851 Z0`

2. Get a thin sheet place it under the homing probe position
	- Paper or shim stock is ideal for this.  You should measure the paper before hand, but most paper is around 0.004" or .1mm thick.

3. Home machine in Z (`G28 Z`)

4. Step up the Z until the paper just clears

	- See the exact Z position with `M114`.

5. Record this value in `M851 Z`

	- E.g. if you measure Z0.6 when the nozzle clears, record `M851 Z0.6`.

## Find Rough X/Y offset of Subsequent Tools

For the purposes of `Z_SAFE_HOMING` and probe sensitivity, I find it useful to roughly center the tool on the bed before probing.  This is primarily an artifact of my Ender 3 bed being unstable at the corners though.

1. Move to a clean section of the bed that is sufficiently rigid

	- Single rail Vslots can be wobbly at the edges, better to move towards the center.

	- Using a round position (ie `X100 Y100`) will make this easier later

2. Create a mark with `T0`

	- for pen tools, a little dot is easy

	- For hotends, paper and a little indent also works well

	- Soft powder is useful, get any sort of indent.  You can also reform it to restart the process

3. Switch to Tool x (ie `T1` or `Tn`)

	- Be sure there is enough Z clearance before you change tools!  Consider bring `T0` up ~5mm.

4. Jog to the approximate location

5. Record the difference in initial position and final position in `M218 Tn X Y`

	- `M114` recalls position

	- Use (Original Position) - (New Position)  to get the offset

	- To avoid moving away from the initial mark, switch back to `T0`, then apply the offset.  Be aware of Z clearance!

6. Check the ballpark estimate by switching back and forth

	- It's often useful to Home (`G28`), as the offset is applied to the current position, causing the `T0` offset to be pushed away from the initial mark.

		- This can be mitigated with by switching to `T0` then applying the offset, but it's easier to just re-home between switches

7. Repeat until you are satisifed with the rough offset.  This is rough, it just needs to be close, we'll fine tune it later.

## Find Z offsets of Subsequent Tools

<!-- Weird edge case: in vanilla (first pass) Marlin, the probing tool needs to be the lowest one.  This seems whack, so what if we use CNC coordinate systems to work around this and use a different offset? -->

CAVEAT: `T1` must be LOWER than `T0` for this to work.  The first Tool must be the highest tool.  A workaround might be possible, or just design your tools better.

1. Home Z of first tool

2. Reset any offset with `M218 T1 Z0`

3. Move `T0` up until there will be sufficient clearance for tool change

4. Move the new tool down until it is zeroed

	- Use a piece of paper or shim stock for this, like in First Tool Z offsetting

5. Take the negative of this to use for `M218 Tn Z`

	- Easiest way to check the offset is to remember the number, switch back to `T0`, then apply new offset.  When switching back to `T1`, the offset will be applied and `T0` shouldn't slam into the bed.

## Fine Tune X/Y offset of Subsequent Tools

Cura's [Calibration Shapes](https://marketplace.ultimaker.com/app/cura/plugins/5axes/CalibrationShapes) plugin has a dual extruder calibration print, which is quite handy (Untested as of 4/28, but i contrigued to the Repo, so I need to shill)

###  Pen tools:

 draw some lines, fine tune the X/Y offsets

 Draw a line in X with both tools, then measure the offset between them.  Repeat and fine tune the offset.  Do the same in Y.

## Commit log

2021-06-01 fix: change Z offset and servo angle
2021-06-01 feat: add Remote_Tilter STLs
    [30mm_Fan_Mount.stl, Direct_Servo_Horn.stl, Direct_Servo_Mount.stl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]
2021-06-01 feat: add Remote_Tilter full CAD
    [Remote_Tilter.f3d]
2021-06-01 docs: Remote_Tilter materials
2021-06-02 feat: add Main_Tilters and HDK Cad models
    [Main_Tilters.f3d, Top_Hat_with_HDK.f3d, Top_Hat_with_HDK.step]
2021-06-02 feat: add Main_Tilters STLs
    [1_Pos_Main.stl, 2_Pos_Main.stl, 4_Pos_Lower.stl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]
2021-06-04 chore: re-orient some STL files
    [Generic_Hat.stl, Nut_Trap.stl]
2021-06-07 chore: update z offset of second extruder
2021-06-07 feat: add limit switch holder
    [New_Limit_switch_holder.stl]
2021-06-07 style: redo folder organization
    [0Main_Tilters.f3d, 0Remote_Tilter.f3d, 0Top_Hat_with_HDK.f3d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]
2021-06-07 feat: add single sided hero me tool
    [Dsub_Cap.stl, Hotend_Mount.stl, Kinematic_Mount.stl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]
2021-06-07 feat: common tools/add ons
    [Camera_Mount.stl, New_Limit_switch_holder.stl, Triple_springs.stl]
2021-06-07 chore: fix hotend offsets, again....
2021-06-07 feat: add double extruder hero me
    [Dsub_Cap_left.stl, Dsub_Cap_right.stl, Fan Duct.stl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]
2021-06-08 style: fix naming convection
    [Fan_Duct.stl, Top_hat.stl]
2021-06-09 docs: add readme's for other CAD folders
2021-06-09 fix: bad link part 2, case sensitive boogaloo
2021-06-10 feat: add Spool Holder files
    [0Spool_Holder.f3d, Bottom_Board_Small.dxf, Fil_Runout_Bottom.stl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]
2021-06-14 feat: printability fixes, mirrored 1_Pos heads
    [1_Pos_Main.stl, 1_Pos_Main_Left.stl, 1_Pos_Main_Right.stl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]
2021-06-14 feat: f3d model for printability, mirror-ability
2021-06-18 feat: no supports needed for X stop
    [New_Limit_switch_holder.stl, Slim_X_Stop.stl, Slim_X_Stop_Support.stl]
2021-06-18 docs: add top level CAD readme
2021-06-21 feat: strain relief for 1 & 2 Pos
    [1_Pos_Main_Left.stl, 1_Pos_Main_Right.stl, 2_Pos_Main.stl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]
2021-06-22 feat: add hot end settings (thermistor+PID)
2021-07-01 feat: add non-symmetric spring options
    [Top_hat.stl, Triple_Springs_Adjustable - Copy.stl]
2021-07-05 style|docs: organize tools, add images
    [Camera_Mount.stl, Triple_Springs_Adjustable.stl, Triple_springs_Static.stl]
2021-07-05 docs: update Single Hero Me readme
    [Kinematic_Mount.stl]
2021-07-06 style: needed materials standaridzation of headers
2021-07-09 feat: more printable remote servo
    [0Remote_Tilter.f3d, 0Remote_Tilter.step, 30mm_Fan_Mount.stl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]
2021-07-14 fix: update probe offsets
2021-07-15 fix: update extruder offsets
2021-07-21 feat: init Marlin config guide
2021-07-21 docs: separate marlin 1 and 2 pos config
2021-07-21 feat: Remote_Tilter orientation
    [30mm_Fan_Mount.stl, Fanless_Nut_Keeper.stl, Horn_Top_Attachment.stl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]
2021-07-21 docs: update R_T readme for fan shroud
2021-07-21 feat: update HDK files
    [0Top_Hat_with_HDK.f3d, 0Top_Hat_with_HDK.step, Top_Hat_with_HDK.step]
2021-07-21 docs: update M_T readme, typos and materials
2021-07-21 feat: raw files (no orientation) for 0.1.1 M_T
    [0Main_Tilters.step, 1_Pos_Main_Left.stl, 1_Pos_Main_Right.stl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]
2021-07-21 feat: M_T printing orientation
    [1_Pos_Main_Right.stl, 2_Pos_Back_Brace.stl, 2_Pos_Main.stl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]
2021-07-21 feat: update fil_runout orientation
    [Fil_Runout_Top.stl]
2021-07-21 feat: X_stop print orientation
    [Slim_X_Stop.stl, Slim_X_Stop_Support.stl]
2021-07-21 feat: Top Tools orientation
    [Triple_Springs_Adjustable.stl, Triple_springs_Static.stl]
2021-07-21 feat: tools print orientation, but only partially
    [Kinematic_Mount.stl, Top_hat.stl]
